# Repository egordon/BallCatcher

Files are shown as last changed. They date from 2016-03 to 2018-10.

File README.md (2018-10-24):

# Ball Catcher
* Car_Lab_CAD: Grouped-up design for holonomic drive. Using quarter-inch acrylic layers and some 3D printed components.
* Car_Lab_Code: Firmware for the PSoC, brains of the chip (includes all Car Lab projects, see BallCatcher folder for that specific project)

## See Ball_Catcher_Final.pdf for full project description

**Abstract:**
In the face of multiple partially-successful attempts in years past, we were determined to build a robot that could catch a ball in real time. We constructed a Holonomic Drive Train that allowed our robot to maneuver at speeds on the order of 6-7 feet per second in any direction, and it could reach those speeds in under a second. Relying on the Pixy Cam, we were able to determine the position of the target ball in 3D space relative to the robot once every 20ms. With a gyroscope, we could keep our robot facing the same direction as it moved to catch the ball. In the end, any ball tossed within a 5-6ft radius of the robot would at very minimum hit the rim. While our robot is far from perfect, we think that we put forward a decent attempt to solve this high-speed, high-percision problem.

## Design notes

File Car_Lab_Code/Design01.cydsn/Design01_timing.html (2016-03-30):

# Static Timing Analysis

Project : | Design01
Build Time : | 03/09/16 16:15:15
Device : | CY8C3866AXI-040
Temperature : | -40C - 85/125C
Vdda : | 5.00
Vddd : | 5.00
Vio0 : | 5.00
Vio1 : | 5.00
Vio2 : | 5.00
Vio3 : | 5.00
Voltage : | 5.0
Vusb : | 5.00

Expand All | Collapse All | Show All Paths | Hide All Paths

+ Timing Violation Section

No Timing Violations

+ Clock Summary Section

Clock | Domain | Nominal Frequency | Required Frequency | Maximum Frequency | Violation
CyILO | CyILO | 1.000 kHz | 1.000 kHz | N/A
CyIMO | CyIMO | 3.000 MHz | 3.000 MHz | N/A
CyMASTER_CLK | CyMASTER_CLK | 24.000 MHz | 24.000 MHz | N/A
CyBUS_CLK | CyMASTER_CLK | 24.000 MHz | 24.000 MHz | N/A
CyPLL_OUT | CyPLL_OUT | 24.000 MHz | 24.000 MHz | N/A

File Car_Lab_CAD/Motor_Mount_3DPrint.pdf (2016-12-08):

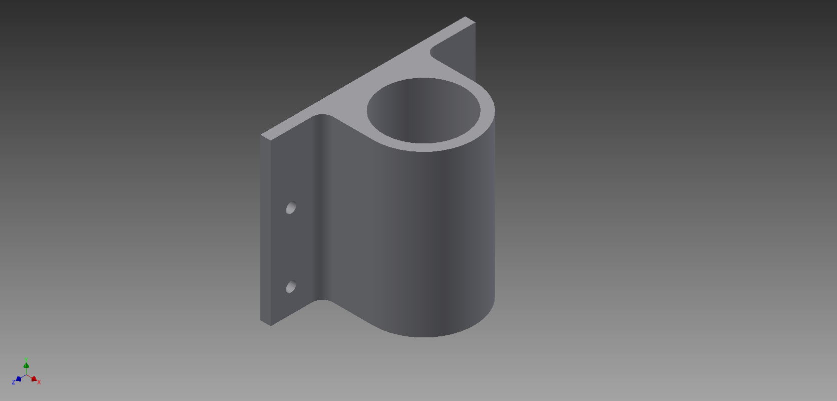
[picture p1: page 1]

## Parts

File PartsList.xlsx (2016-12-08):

Description | Vendor | URL | Part No. | Quantity | Unit Cost | Cost | Memo
4.5m Range Ultrasonic Rangefinder | Maxbotix | http://maxbotix.com/Ultrasonic_Sensors/MB1220.htm | MB1220 XL-MaxSonar-EZ2 | 1 | $39.95 | $39.95 | Worst case 3m, Best case 6m
Pan/Tilt Mount for Pixy Cam w/ Servos | RobotShop | http://robotshop.com/en/pan-tilt-kit-pixy-cmucam5-image-sensor.html | RB-Cha-02 | 1 | $32.00 | $32.00 | Includes 180 degree servos.
Net for catching ball. | Amazon | http://amazon.com/Spalding-All-Weather-Basketball-Net-White/dp/B000H38LLU | Basketball Net | 1 | $3.49 | $3.49 | Might need to cut it.
Purple 4" Foam Ball | Amazon | http://www.amazon.com/POOF-240BL-4-Inch-Foam-Ball/dp/B004MQ5BAM | 4-Inch Foam Ball | 1 | $2.79 | $2.79 | Small enough to definitely fit in net.
Orange 5" Foam Basketball | Amazon | http://www.amazon.com/SKLZ-Mini-Swish-Foam-Ball/dp/B00MOIQCG2 | 5-inch Mini Basketball | 1 | $5.99 | $5.99 | Easier to track, but might not fit well in net.
4" Omni Wheel | Vex | http://www.vexrobotics.com/omni-wheels.html | 217-2584 | 4 | $17.99 | $71.96 | Cheapest wheel for this radius, 1.4in bolt circle with 0.13in holes, self-tap with #8 screw (0.16" thread diameter).
6V Gearmotor | Polulu | https://www.pololu.com/product/1572 | 1572 | 4 | $21.95 | $87.80 | 20.4:1 Ratio, 460 RPM at 75 oz-in, ~10 ft/s^2 acceleration for 7lb bot, ~8 ft/s free speed, provides ~13 ft catch radius for 2s flight time, mount with 2 M3
4mm 4-40 Universal Hub (2-Pck) | Polulu | https://www.pololu.com/product/1081 | 1081 | 2 | $6.95 | $13.90 | 4mm Shaft to 0.25in 4-40 bolt ring
Pixy Camera | N/A | N/A | N/A | 1 | $0.00 | $0.00 | Already Have
Laser Sight | N/A | N/A | N/A | 1 | $0.00 | $0.00 | Used for Debugging, Rad Has
 |  |  |  |  | Total: | $257.88
Notes:
Will need 2 M3 bolts to mount motor to acryllic.
Will cut acryllic as adapter between 0.25in 4-40 bolt circle and 1.4in #8 bolt circle.
Will need 3 #8 self-tap screws to attach acryllic adapter to omni-wheels.

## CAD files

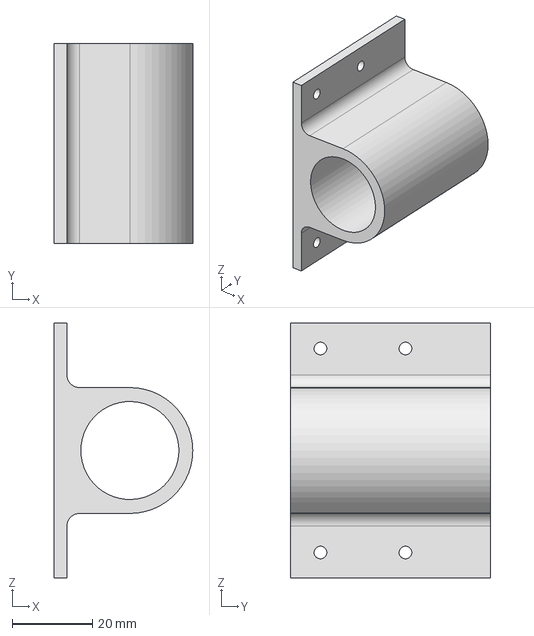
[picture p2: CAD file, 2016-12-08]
Car_Lab_CAD/Motor_Mount_3DPrint.stp
34.5 x 49.8 x 63.5 mm

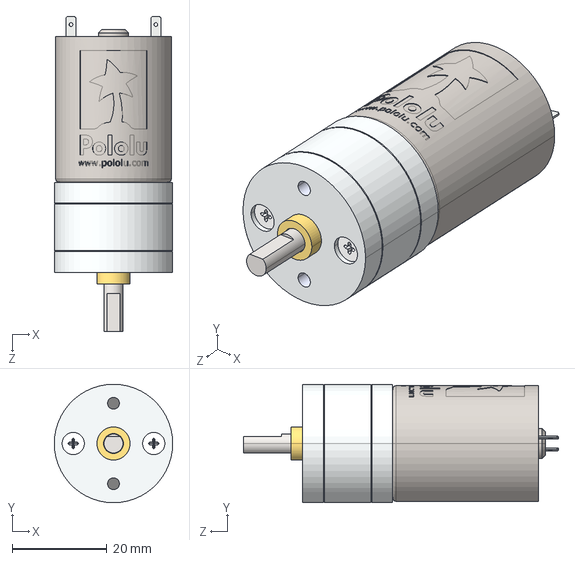
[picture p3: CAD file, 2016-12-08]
Car_Lab_CAD/25d-metal-gearmotor-20.4.step
25.0 x 25.0 x 66.5 mm

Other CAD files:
Car_Lab_CAD/Motor_Mount_Acryllic.dwg
Car_Lab_CAD/LayerTwo_Acryllic.dwg
Car_Lab_CAD/Camera_Mount_Acryllic.dwg
Car_Lab_CAD/Rim_Acryllic.dwg
Car_Lab_CAD/Hub_Adapter_Acryllic.dwg
Car_Lab_CAD/BallCatcher.iam
Car_Lab_CAD/Base_Acryllic.ipt
Car_Lab_CAD/Camera_Mount_Acryllic.ipt
Car_Lab_CAD/Hex_Standoff.ipt
Car_Lab_CAD/Hex_Standoff_CPY.ipt
Car_Lab_CAD/Hex_Standoff_CPY1.ipt
Car_Lab_CAD/Hex_Standoff_CPY_CPY.ipt
Car_Lab_CAD/Hub_Adapter_Acryllic.ipt
Car_Lab_CAD/Imported Components/Vex_Omni_Wheel_4in/217-2584-001 Rev1.ipt
Car_Lab_CAD/Imported Components/Vex_Omni_Wheel_4in/217-2584-002 Rev2.ipt
Car_Lab_CAD/Imported Components/Vex_Omni_Wheel_4in/217-2584-003 Rev4.ipt
Car_Lab_CAD/Imported Components/Vex_Omni_Wheel_4in/217-2584-004 Rev1.ipt
Car_Lab_CAD/Imported Components/Vex_Omni_Wheel_4in/217-2584-005 Rev1 A.ipt
Car_Lab_CAD/Imported Components/Vex_Omni_Wheel_4in/90116A020_90116A020.ipt
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

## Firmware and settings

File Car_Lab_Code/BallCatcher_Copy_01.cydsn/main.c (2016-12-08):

/* ========================================
 *
 * Car Lab 2016: Independent Project
 * Ethan Gordon, Luke Pfleger
 *
 * Goal: Catch a ball.
 *
 * ========================================
*/
#include <device.h>
#include <stdio.h>
#include <math.h>
#include "drivetrain.h"

/* Pixy Params */
static short xScreen = 0;
static short yScreen = 0;
static short width = 0;
static short height = 0;

/* UART States */
#define STATE_SYNC 0
#define STATE_READ 1

/* Offsets */
#define X_OFFSET 160
#define Y_OFFSET 100

#define GYRO_SET 24425

#define GYRO_DEADBAND 30

/* Constants */
#define PI 3.14159f
#define GRAVITY 386.1f /* in/s^2 */
#define ALPHA 0.05f
#define ALPHAZ 0.2f


/* Trig Functions */
#define COS(x) (1 - (x)*(x)/2.0f)
#define SIN(x) ((x) - (x)*(x)*(x)/6.0f )
#define DEG(x) (x)*(180.0f / 3.14159f)
#define RAD(x) (x)*(3.14159f / 180.0f)

static int watchdog = 0;

/* Read data from the Pixy Cam */
static int dataRead = 0;
CY_ISR(uart)
{
    static int state = STATE_SYNC;
    static short word = 0;
    static int readPos = 0;
    
    unsigned char byte = Pixy_UART_GetChar();
    
    if (state == STATE_SYNC) {
        switch (readPos) {
        case 0:
            readPos = (byte == 0x55) ? 1 : 0;
            break;
        case 1:
            readPos = (byte == 0xaa) ? 2 : 0;
            break;
        case 2:
            if (byte == 0x55) {
                readPos = 3;
            } else {
                word = byte;
                readPos = 1;
                state = STATE_READ;
            }
            break;
        case 3:
            readPos = 0;
            state = (byte == 0xaa) ? STATE_READ : STATE_SYNC;
        break;
        default:
            readPos = 0;
        }
    } else { 
        if (readPos%2) {
            word += (((short)byte) << 8);
            switch(readPos){
            case 5:
                xScreen = word;
            break;
            case 7:
                yScreen = word;
            break;
            case 9:
                width = word;
            break;
            case 11:
                height = word;
                state = STATE_SYNC;
                readPos = -1;
                dataRead = 1;
                watchdog = 0;
            break;
            }
        } else {
            word = byte;
        }
        readPos++;
    }
    
}

/* Read Gyro Data */
static int gyro = GYRO_SET;
CY_ISR(analog_isr)
{
    gyro = ADC_GetResult16();
}

/* Read the pan and tilt data from Pixy cam */
static float pan = 0.0f;

CY_ISR(pan_isr)
{
    int panRead = (int)PanTime_ReadCapture();
    pan = (float)(panRead) * 0.0967049f - 799.878f; /* Linear Interpolation from Wolfram */
    Pan_Reset_Write(1);
}

static float tilt = 0;

CY_ISR(tilt_isr)
{
    int tiltRead = (int)TiltTime_ReadCapture();
    tilt = 2.0f * ((float)(tiltRead) * 0.0367647f - 289.154f); /* Linear Interpolation from Wolfram */
    if(tilt > 40.0f) tilt = 40.0f;
    Tilt_Reset_Write(1);
}

/* Spherical */
static float r = 0.0f;
static float phi = 0.0f;
static float theta = 0.0f;

static float dr = 0.0f;
static float dphi = 0.0f;
static float dtheta = 0.0f;

CY_ISR(clk_isr)
{
    char tstr[17] = {0};
    static float rPrev = 0.0f;
    static float phiPrev = 0.0f;
    static float thetaPrev = 0.0f;
    
    watchdog++;
    
    if(dataRead) {
        float tanTheta, camTheta, heightPredicted;
        dataRead = 0;
    
        /* Calculate Spherical Radius */
        r = (320.0f * 7.0f) / (2.0f * (float)(width) * 0.767f); /* r = pix * diameter / (pixWidth * 2*tan(75/2)) */
        dr = 50.0f * (r - rPrev);
        rPrev = r;
        
        /* Calculate Theta, include Camera Tilt and Y position */
        heightPredicted = (1481.14075f) / r;
        tanTheta = (7.0f * (yScreen - Y_OFFSET)) / (r * heightPredicted);
        camTheta = DEG(tanTheta*tanTheta*tanTheta / 3.0f - tanTheta);
        if ((camTheta < 2.0f) && (camTheta > -2.0f)) camTheta = 0.0f;
        if (tilt < 0.0f)
            theta = 0.0f;
        else theta = tilt + camTheta;
        dtheta = 50.0f * (theta - thetaPrev);
        thetaPrev = theta;
        
        /* Calculate Phi, ignore X location, only use Camera Pan */
        phi = pan;
        dphi = (phi - phiPrev) * 50.0f;
        phiPrev = phi;
        
    }
}

void main()
{
    int finished = 0;
    char tstr[17] = {0};
    
    /* Start STUFFZ */
    DriveTrain_Start();
    LCD_Start();
    ADC_Start();
    ADC_StartConvert();
    
    /* Start Counters */
    PanTime_Start();
    TiltTime_Start();
    
    /* Interrupts */
    Pixy_int_Start();
    Pixy_int_SetVector(uart);
    Pan_int_Start();
    Pan_int_SetVector(pan_isr);
    Tilt_int_Start();
    Tilt_int_SetVector(tilt_isr);
    Clk_int_Start();
    Clk_int_SetVector(clk_isr);
    Analog_int_Start();
    Analog_int_SetVector(analog_isr);
    
    /* Start UART */
    Pixy_UART_Start();

    CyGlobalIntEnable;
    while(!finished)
    {
        float z, dz, x, dx, y, dy, dxMeas, dyMeas, dzMeas, radical, tol, kpx;
        static float xTarget = 0.0f;
        static float yTarget = 0.0f;
        
        float gyro_err, gyro_p, gyro_i;
        static float gyro_sum = 0.0f;
    
        z = r * SIN(RAD(theta));
        dzMeas = dr * SIN(RAD(theta)) + r*COS(RAD(theta))*RAD(dtheta);
        
        x = r * COS(RAD(theta)) * COS(RAD(phi)) - 9.0f; /* Center on center of basket */
        dxMeas = dr * COS(RAD(theta)) * COS(RAD(phi)) - r * SIN(RAD(theta)) * COS(RAD(phi))*RAD(dtheta) - r * COS(RAD(theta)) * SIN(RAD(phi))*RAD(dphi);
    
        y = -r * COS(RAD(theta)) * SIN(RAD(phi));
        dyMeas = -dr * COS(RAD(theta)) * SIN(RAD(phi)) + r * SIN(RAD(theta)) * SIN(RAD(phi))*RAD(dtheta) - r * COS(RAD(theta)) * COS(RAD(phi))*RAD(dphi);
        
        /* Average Velocities */
        if (dyMeas > 60.0f) dyMeas = 0.0f;
        if (dyMeas < -60.0f) dyMeas = 0.0f;
        if (dxMeas > 60.0f) dxMeas = 0.0f;
        if (dxMeas < -60.0f) dxMeas = 0.0f;
        if(z < 3.0f) {
            dx = dxMeas;
            dy = dyMeas;
        } else {
            dx = ALPHA*dxMeas + (1.0f-ALPHA)*dx;
            dy = ALPHA*dyMeas + (1.0f-ALPHA)*dy;
        }
        dz = ALPHAZ*dzMeas + (1.0f-ALPHAZ)*dz;
        
        radical = dz * dz + 2.0f*GRAVITY*z;
        if(radical < 0)
            tol = 0.0f;
        else
            tol = (dz + (float)sqrt((double)radical)) / GRAVITY;
            
        xTarget = x + tol*dx;
        yTarget = y + tol*dy;
            
        sprintf(tstr, "x: %+2.2f  ", xTarget);
        
        LCD_Position(0, 0);
        LCD_PrintString(tstr);
        
        
        sprintf(tstr, "y: %+2.2f  ", yTarget);
        
        LCD_Position(1, 0);
        LCD_PrintString(tstr);
        
        /* Gyro PID Loop */
        gyro_err = gyro - GYRO_SET;
        if ((gyro_err < GYRO_DEADBAND) && (gyro_err > -GYRO_DEADBAND))
            gyro_err = 0;
        gyro_p = 0.5f * gyro_err;
        
        gyro_sum += gyro_err;
        /* Clamp Sum */
        if (gyro_sum > 10000) gyro_sum = 10000;
        else if (gyro_sum < -10000) gyro_sum = -10000;
        gyro_i = 0.01f * gyro_sum;
        
        if (xTarget < 0)
            kpx = 100.0f;
        else kpx = 35.0f;
        
        if ((tilt > 10.0f) && (watchdog < 10)) {
            DriveTrain_Set(-45.0f * yTarget, kpx * xTarget, (int)(gyro_p + gyro_i));
        } else DriveTrain_Stop();
        
    }
    
    /* Stop Drive Train */
    DriveTrain_Stop();
    
    for(;;){}
}

/* [] END OF FILE */

/* Saved Junk
static float xLast = 0.0f;
    static float yLast = 0.0f;
    static float zLast = 0.0f;
    if (width != 0 && height != 0)
    {
        float tanPhi, tanTheta, xDotTest, yDotTest, zDotTest, r, phi, theta;
        float tof;
        r = (320.0f * 7.0f) / (2.0f * (float)(width) * 0.767f);
        tanPhi = (7.0f * (x - X_OFFSET)) / (r * width);
        tanTheta = (7.0f * (y - Y_OFFSET)) / (r * height);
        phi = pan + (tanPhi - tanPhi*tanPhi*tanPhi / 3) * (180.0f / PI);
        theta = tilt - (tanTheta - tanTheta*tanTheta*tanTheta / 3) * (180.0f / PI);

        
        xBall = r * cos(theta * PI / 180.0f) * cos(phi * PI / 180.0f);
        yBall = r * cos(theta * PI / 180.0f) * sin(phi * PI / 180.0f);
        zBall = r * sin(theta * PI / 180.0f);
        
        if ((xBall - xLast > 100) || (xBall - xLast < -100)) xBall = xLast;
        if ((yBall - yLast > 100) || (yBall - yLast < -100)) yBall = yLast;
        if ((zBall - zLast > 50) || (zBall - zLast < -50)) zBall = zLast;
        

        xDotTest = (xBall - xLast) * 50.0f;
        yDotTest = (yBall - yLast) * 50.0f;
        zDotTest = (zBall - zLast) * 50.0f;
        
        xDot = ALPHA*xDotTest + (1 - ALPHA)*xDot;
        yDot = ALPHA*yDotTest + (1 - ALPHA)*yDot;
        zDot = ALPHA*zDotTest + (1 - ALPHA)*zDot;
        
        xLast = xBall;
        yLast = yBall;
        zLast = zBall;
        

        tof = (zDot + sqrt(zDot*zDot + 2*GRAVITY*zBall)) / GRAVITY;
        xTarget = xBall + tof*xDot;
        yTarget = yBall + tof*yDot;
    }
    */

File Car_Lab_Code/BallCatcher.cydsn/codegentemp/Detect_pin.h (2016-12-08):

/*******************************************************************************
* File Name: Detect_pin.h  
* Version 1.70
*
* Description:
*  This file containts Control Register function prototypes and register defines
*
* Note:
*
********************************************************************************
* Copyright 2008-2010, Cypress Semiconductor Corporation.  All rights reserved.
* You may use this file only in accordance with the license, terms, conditions, 
* disclaimers, and limitations in the end user license agreement accompanying 
* the software package with which this file was provided.
********************************************************************************/

#if !defined(CY_PINS_Detect_pin_H) /* Pins Detect_pin_H */
#define CY_PINS_Detect_pin_H

#include "cytypes.h"
#include "cyfitter.h"
#include "cypins.h"
#include "Detect_pin_aliases.h"


/***************************************
*        Function Prototypes             
***************************************/    

void    Detect_pin_Write(uint8 value) ;
void    Detect_pin_SetDriveMode(uint8 mode) ;
uint8   Detect_pin_ReadDataReg(void) ;
uint8   Detect_pin_Read(void) ;
uint8   Detect_pin_ClearInterrupt(void) ;

/***************************************
*           API Constants        
***************************************/

/* Drive Modes */
#define Detect_pin_DM_ALG_HIZ         PIN_DM_ALG_HIZ
#define Detect_pin_DM_DIG_HIZ         PIN_DM_DIG_HIZ
#define Detect_pin_DM_RES_UP          PIN_DM_RES_UP
#define Detect_pin_DM_RES_DWN         PIN_DM_RES_DWN
#define Detect_pin_DM_OD_LO           PIN_DM_OD_LO
#define Detect_pin_DM_OD_HI           PIN_DM_OD_HI
#define Detect_pin_DM_STRONG          PIN_DM_STRONG
#define Detect_pin_DM_RES_UPDWN       PIN_DM_RES_UPDWN

/* Digital Port Constants */
#define Detect_pin_MASK               Detect_pin__MASK
#define Detect_pin_SHIFT              Detect_pin__SHIFT
#define Detect_pin_WIDTH              1u

/***************************************
*             Registers        
***************************************/

/* Main Port Registers */
/* Pin State */
#define Detect_pin_PS                     (* (reg8 *) Detect_pin__PS)
/* Data Register */
#define Detect_pin_DR                     (* (reg8 *) Detect_pin__DR)
/* Port Number */
#define Detect_pin_PRT_NUM                (* (reg8 *) Detect_pin__PRT) 
/* Connect to Analog Globals */                                                  
#define Detect_pin_AG                     (* (reg8 *) Detect_pin__AG)                       
/* Analog MUX bux enable */
#define Detect_pin_AMUX                   (* (reg8 *) Detect_pin__AMUX) 
/* Bidirectional Enable */                                                        
#define Detect_pin_BIE                    (* (reg8 *) Detect_pin__BIE)
/* Bit-mask for Aliased Register Access */
#define Detect_pin_BIT_MASK               (* (reg8 *) Detect_pin__BIT_MASK)
/* Bypass Enable */
#define Detect_pin_BYP                    (* (reg8 *) Detect_pin__BYP)
/* Port wide control signals */                                                   
#define Detect_pin_CTL                    (* (reg8 *) Detect_pin__CTL)
/* Drive Modes */
#define Detect_pin_DM0                    (* (reg8 *) Detect_pin__DM0) 
#define Detect_pin_DM1                    (* (reg8 *) Detect_pin__DM1)
#define Detect_pin_DM2                    (* (reg8 *) Detect_pin__DM2) 
/* Input Buffer Disable Override */
#define Detect_pin_INP_DIS                (* (reg8 *) Detect_pin__INP_DIS)
/* LCD Common or Segment Drive */
#define Detect_pin_LCD_COM_SEG            (* (reg8 *) Detect_pin__LCD_COM_SEG)
/* Enable Segment LCD */
#define Detect_pin_LCD_EN                 (* (reg8 *) Detect_pin__LCD_EN)
/* Slew Rate Control */
#define Detect_pin_SLW                    (* (reg8 *) Detect_pin__SLW)

/* DSI Port Registers */
/* Global DSI Select Register */
#define Detect_pin_PRTDSI__CAPS_SEL       (* (reg8 *) Detect_pin__PRTDSI__CAPS_SEL) 
/* Double Sync Enable */
#define Detect_pin_PRTDSI__DBL_SYNC_IN    (* (reg8 *) Detect_pin__PRTDSI__DBL_SYNC_IN) 
/* Output Enable Select Drive Strength */
#define Detect_pin_PRTDSI__OE_SEL0        (* (reg8 *) Detect_pin__PRTDSI__OE_SEL0) 
#define Detect_pin_PRTDSI__OE_SEL1        (* (reg8 *) Detect_pin__PRTDSI__OE_SEL1) 
/* Port Pin Output Select Registers */
#define Detect_pin_PRTDSI__OUT_SEL0       (* (reg8 *) Detect_pin__PRTDSI__OUT_SEL0) 
#define Detect_pin_PRTDSI__OUT_SEL1       (* (reg8 *) Detect_pin__PRTDSI__OUT_SEL1) 
/* Sync Output Enable Registers */
#define Detect_pin_PRTDSI__SYNC_OUT       (* (reg8 *) Detect_pin__PRTDSI__SYNC_OUT) 


#if defined(Detect_pin__INTSTAT)  /* Interrupt Registers */

    #define Detect_pin_INTSTAT                (* (reg8 *) Detect_pin__INTSTAT)
    #define Detect_pin_SNAP                   (* (reg8 *) Detect_pin__SNAP)

#endif /* Interrupt Registers */

#endif /* End Pins Detect_pin_H */


/* [] END OF FILE */

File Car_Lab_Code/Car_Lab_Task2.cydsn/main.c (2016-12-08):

/* ========================================
 *
 * Copyright Ethan Gordon, Luke Pfleger, 2016
 * Car Lab, Task 2
 * Line Follower
 *
 * Goal: Follow a line for 2 laps.
 * ========================================
*/
#include <device.h>
#include <stdio.h>

/* State Estimation */
#include "state.h"

/* Angle Actuation */
#include "angle.h"

/* PID Loop */
#include "pid.h"

/* Constants */
#define ALPHA 0.2f
/* Total Circumference = 20cm = 0.656168 ft */
/* 5 Magnets per Revolution: 0.656168 / 5 = 0.1312336 ft */
#define MAG_DIST 0.1312336f
#define SECOND 1000
#define TICKS_PER_LAB 730
#define LAPS 2

/* Direction Detection */
#define DIR_ANG 20
#define DIR_CAP 60
#define DIR_THRESH 5


/** Changeable Constants **/
#define SPD_KP  600.0f
#define SPD_KI  0.8f
#define SPD_SETPOINT 4.0f

#define AVG_KP_DEF 0.58f
static float AVG_KP = AVG_KP_DEF;
#define AVG_SETPOINT 720

#define ANG_KP  0.0f
#define ANG_SETPOINT 0

/** END Changeable Constants **/

/* Macros */
#define ABS(x)  ( ( (x) < 0) ? -(x) : (x) )


/* State Estimators */
State_T spdState = NULL;

/* PID Loops */
PID_T spdPID = NULL;

/* UART Debug Interrupt */
static int16 dataArr[3500] = {0};
int restart = 1;
CY_ISR(uart)
{
    int i, j;
    char c = UART_GetChar();
    if(c == 'd') {
        /* Output Error Data from Last Run */
        for(i = 0; i < 3500; i++) {
            char tstr[9] = {0};
            if(i < 3499) sprintf(tstr, "%+4d, ", dataArr[i]);
            else sprintf(tstr, "%+4d", dataArr[i]);
            for(j = 0; j < 8; j++)
                UART_PutChar(tstr[j]);
        }
    } else if (c == '+') {
        /* Increase Kp */
        char tstr[11] = {0};
        AVG_KP += 0.05f;
        sprintf(tstr, "\nKp=%1.2f, ", AVG_KP);
        for(j = 0; j < 10; j++)
            UART_PutChar(tstr[j]);
    } else if (c == '-') {
        /* Decrease Kp */
        char tstr[11] = {0};
        AVG_KP -= 0.01f;
        sprintf(tstr, "\nKp=%1.2f, ", AVG_KP);
        for(j = 0; j < 10; j++)
            UART_PutChar(tstr[j]);
    } else if (c == 'k') {
        /* Reset Kp to Default */
        char tstr[11] = {0};
        AVG_KP = AVG_KP_DEF;
        sprintf(tstr, "\nKp=%1.2f, ", AVG_KP);
        for(j = 0; j < 10; j++)
            UART_PutChar(tstr[j]);
    } else if (c == 'r') {
        /* Start New Run */
        restart = 1;
    }

}

/* Clock and Clock Interrupt */
int millis = 0;
CY_ISR(clk)
{
    millis++;

    /* Watchdog Functions */
    State_Watchdog(spdState);
}

/* Line Interrupts */
static int topLineX = AVG_SETPOINT / 2;
static int linePos = AVG_SETPOINT / 2;
static int isLineLost = 0;

CY_ISR(timer)
{
    isLineLost = 0;
    topLineX = Line_Timer_ReadCapture();
    if (topLineX > 67)
        linePos = topLineX;
    else isLineLost = 1;
}

static int botLineX = AVG_SETPOINT;
static int linePosBot = AVG_SETPOINT;
CY_ISR(timer_bot)
{
    botLineX = Line_Timer_bot_ReadCapture();
    if (botLineX > 67)
        linePosBot = botLineX;
    else isLineLost = 1;
}

/* Hall Effect Interrupt */
static int ticks = 0;
CY_ISR(spd)
{
    static int lastTime = 0;
    int currentTime = millis;

    /* Update State Estimate */
    if (lastTime != 0) {
        State_Update(spdState, (MAG_DIST * 1000.0f)/((float)(currentTime - lastTime)));
    }
    lastTime = currentTime;
    ticks++;
}

void main()
{

    /* LCD Display */
    char tstr[17] = {0};

    CyGlobalIntEnable;

    /***** Firmware Declarations *****/

    /* Start Reference */
    VRef_Start();

    /* Start Comparator */
    Thresholder_Start();

    /* Start Counters */
    Counter_Start();
    LineCounter_Start();
    Line_Timer_Start();
    LineCounter_bot_Start();
    Line_Timer_bot_Start();

    /* Start LCD */
    LCD_Start();

    /* Start PWM */
    MOSFET_Start();
    Angle_Start();

    /* Start UART */
    UART_Start();

    /***** End Firmware Declarations *****/

    /***** Object Declarations *****/

    /* Start Speed State Estimator */
    spdState = State_Alloc();
    State_Start(spdState, ALPHA, 0.0f, SECOND);

    /* Start Speed PID Loop */
    spdPID = PID_Alloc();
    PID_Start(spdPID, SPD_KP, SPD_KI, 0.0f, (float)(MOSFET_ReadPeriod() + 1));

    /***** End Object Declarations *****/

    /***** Interrupt Declarations *****/

    /* Clock Interrupt */
    clk_inter_Start();
    clk_inter_SetVector(clk);

    /* Line Timer Interrupt */
    timer_inter_Start();
    timer_inter_SetVector(timer);
    timer_inter_bot_Start();
    timer_inter_bot_SetVector(timer_bot);

    /* UART Interrupt */
    uart_rx_Start();
    uart_rx_SetVector(uart);


    /* Speed Interrupt */
    spd_inter_Start();
    spd_inter_SetVector(spd);
    /***** End Interrupt Declarations *****/

    /*** Set PID Setpoints ***/
    for(;;) {
        int i = 0;
        int dir = 0;
        /* Wait for Serial Restart */
        while(!restart) {
            LCD_Position(1, 0);
            LCD_PrintString("Wait on Restart");
        }
        /* 4 Second Delay */
        {
            int targetmillis = millis + 4000;
            LCD_Position(1, 0);
            LCD_PrintString("Starting........");
            while(millis < targetmillis);
        }
        ticks = 0;
        restart = 0;
        PID_Setpoint(spdPID, SPD_SETPOINT);

        while(ticks < (TICKS_PER_LAB * LAPS))
        {
            int16 err, avg, ang;

            /* Update PID Loop */
            PID_Update(spdPID, State_Avg(spdState), 1);
            avg = linePos + linePosBot;
            ang = linePos - linePosBot;

            /**** Direction Detection ****/
            if (!isLineLost) {
                if(ang > DIR_ANG) {
                    dir += 2;
                } else if (ang < -DIR_ANG) {
                    dir -= 2;
                } else {
                    if(dir > 0) dir--;
                    else dir++;
                }
            }

            /* Clamp Direction Variable */
            if (dir < -DIR_CAP) dir = -DIR_CAP;
            if (dir > DIR_CAP) dir = DIR_CAP;

            if (dir > DIR_THRESH) { /* LEFT: Use left-most point. */
                if (linePos > linePosBot)
                    avg = linePos + linePos;
                else avg = linePosBot + linePosBot;
            } else if (dir < -DIR_THRESH) { /* RIGHT: Use right-most point. */
                if (linePos < linePosBot)
                    avg = linePos + linePos;
                else avg = linePosBot + linePosBot;
            } /* Else STRAIGHT: Use average of points. */

            /*** END Direction Detection ***/
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

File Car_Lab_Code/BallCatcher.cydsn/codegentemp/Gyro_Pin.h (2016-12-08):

/*******************************************************************************
* File Name: Gyro_Pin.h  
* Version 1.70
*
* Description:
*  This file containts Control Register function prototypes and register defines
*
* Note:
*
********************************************************************************
* Copyright 2008-2010, Cypress Semiconductor Corporation.  All rights reserved.
* You may use this file only in accordance with the license, terms, conditions, 
* disclaimers, and limitations in the end user license agreement accompanying 
* the software package with which this file was provided.
********************************************************************************/

#if !defined(CY_PINS_Gyro_Pin_H) /* Pins Gyro_Pin_H */
#define CY_PINS_Gyro_Pin_H

#include "cytypes.h"
#include "cyfitter.h"
#include "cypins.h"
#include "Gyro_Pin_aliases.h"


/***************************************
*        Function Prototypes             
***************************************/    

void    Gyro_Pin_Write(uint8 value) ;
void    Gyro_Pin_SetDriveMode(uint8 mode) ;
uint8   Gyro_Pin_ReadDataReg(void) ;
uint8   Gyro_Pin_Read(void) ;
uint8   Gyro_Pin_ClearInterrupt(void) ;

/***************************************
*           API Constants        
***************************************/

/* Drive Modes */
#define Gyro_Pin_DM_ALG_HIZ         PIN_DM_ALG_HIZ
#define Gyro_Pin_DM_DIG_HIZ         PIN_DM_DIG_HIZ
#define Gyro_Pin_DM_RES_UP          PIN_DM_RES_UP
#define Gyro_Pin_DM_RES_DWN         PIN_DM_RES_DWN
#define Gyro_Pin_DM_OD_LO           PIN_DM_OD_LO
#define Gyro_Pin_DM_OD_HI           PIN_DM_OD_HI
#define Gyro_Pin_DM_STRONG          PIN_DM_STRONG
#define Gyro_Pin_DM_RES_UPDWN       PIN_DM_RES_UPDWN

/* Digital Port Constants */
#define Gyro_Pin_MASK               Gyro_Pin__MASK
#define Gyro_Pin_SHIFT              Gyro_Pin__SHIFT
#define Gyro_Pin_WIDTH              1u

/***************************************
*             Registers        
***************************************/

/* Main Port Registers */
/* Pin State */
#define Gyro_Pin_PS                     (* (reg8 *) Gyro_Pin__PS)
/* Data Register */
#define Gyro_Pin_DR                     (* (reg8 *) Gyro_Pin__DR)
/* Port Number */
#define Gyro_Pin_PRT_NUM                (* (reg8 *) Gyro_Pin__PRT) 
/* Connect to Analog Globals */                                                  
#define Gyro_Pin_AG                     (* (reg8 *) Gyro_Pin__AG)                       
/* Analog MUX bux enable */
#define Gyro_Pin_AMUX                   (* (reg8 *) Gyro_Pin__AMUX) 
/* Bidirectional Enable */                                                        
#define Gyro_Pin_BIE                    (* (reg8 *) Gyro_Pin__BIE)
/* Bit-mask for Aliased Register Access */
#define Gyro_Pin_BIT_MASK               (* (reg8 *) Gyro_Pin__BIT_MASK)
/* Bypass Enable */
#define Gyro_Pin_BYP                    (* (reg8 *) Gyro_Pin__BYP)
/* Port wide control signals */                                                   
#define Gyro_Pin_CTL                    (* (reg8 *) Gyro_Pin__CTL)
/* Drive Modes */
#define Gyro_Pin_DM0                    (* (reg8 *) Gyro_Pin__DM0) 
#define Gyro_Pin_DM1                    (* (reg8 *) Gyro_Pin__DM1)
#define Gyro_Pin_DM2                    (* (reg8 *) Gyro_Pin__DM2) 
/* Input Buffer Disable Override */
#define Gyro_Pin_INP_DIS                (* (reg8 *) Gyro_Pin__INP_DIS)
/* LCD Common or Segment Drive */
#define Gyro_Pin_LCD_COM_SEG            (* (reg8 *) Gyro_Pin__LCD_COM_SEG)
/* Enable Segment LCD */
#define Gyro_Pin_LCD_EN                 (* (reg8 *) Gyro_Pin__LCD_EN)
/* Slew Rate Control */
#define Gyro_Pin_SLW                    (* (reg8 *) Gyro_Pin__SLW)

/* DSI Port Registers */
/* Global DSI Select Register */
#define Gyro_Pin_PRTDSI__CAPS_SEL       (* (reg8 *) Gyro_Pin__PRTDSI__CAPS_SEL) 
/* Double Sync Enable */
#define Gyro_Pin_PRTDSI__DBL_SYNC_IN    (* (reg8 *) Gyro_Pin__PRTDSI__DBL_SYNC_IN) 
/* Output Enable Select Drive Strength */
#define Gyro_Pin_PRTDSI__OE_SEL0        (* (reg8 *) Gyro_Pin__PRTDSI__OE_SEL0) 
#define Gyro_Pin_PRTDSI__OE_SEL1        (* (reg8 *) Gyro_Pin__PRTDSI__OE_SEL1) 
/* Port Pin Output Select Registers */
#define Gyro_Pin_PRTDSI__OUT_SEL0       (* (reg8 *) Gyro_Pin__PRTDSI__OUT_SEL0) 
#define Gyro_Pin_PRTDSI__OUT_SEL1       (* (reg8 *) Gyro_Pin__PRTDSI__OUT_SEL1) 
/* Sync Output Enable Registers */
#define Gyro_Pin_PRTDSI__SYNC_OUT       (* (reg8 *) Gyro_Pin__PRTDSI__SYNC_OUT) 


#if defined(Gyro_Pin__INTSTAT)  /* Interrupt Registers */

    #define Gyro_Pin_INTSTAT                (* (reg8 *) Gyro_Pin__INTSTAT)
    #define Gyro_Pin_SNAP                   (* (reg8 *) Gyro_Pin__SNAP)

#endif /* Interrupt Registers */

#endif /* End Pins Gyro_Pin_H */


/* [] END OF FILE */

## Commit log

2016-03-30 Initial Code Upload
    [Base_Acryllic.0001.ipt, Base_Acryllic.ipt]
2016-03-30 Switched to slower speed, prettied up magic numbers
